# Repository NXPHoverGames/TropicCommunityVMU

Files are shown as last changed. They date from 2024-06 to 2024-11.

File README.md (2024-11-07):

# Tropic Community VMU

Tropic Community VMU (Vehicle Management Unit) is an BSD-3 Licensed Open-Source base board designed around the [Teensy 4.1 Development board](https://www.pjrc.com/store/teensy41.html).

> [!NOTE]  
> Tropic VMU is a project created by a group of passionate individuals who work on it in their free time. It's important for users to understand that Tropic might not provide the same reliability, features, or support as products from well-established companies. Using Tropic is entirely up to the user's discretion and comes with its own risks.
> 
> For a more dependable and professional VMU, we suggest looking into the NXP reference based on Dronecode Pixhawk standard V6X-RT (p/n MR-VMU-RT1176). The NXP V6X-RT offers advanced features, some level of support across multiple autopilots, and is designed towards the needs of professional users, providing a more reliable solution for their requirements.

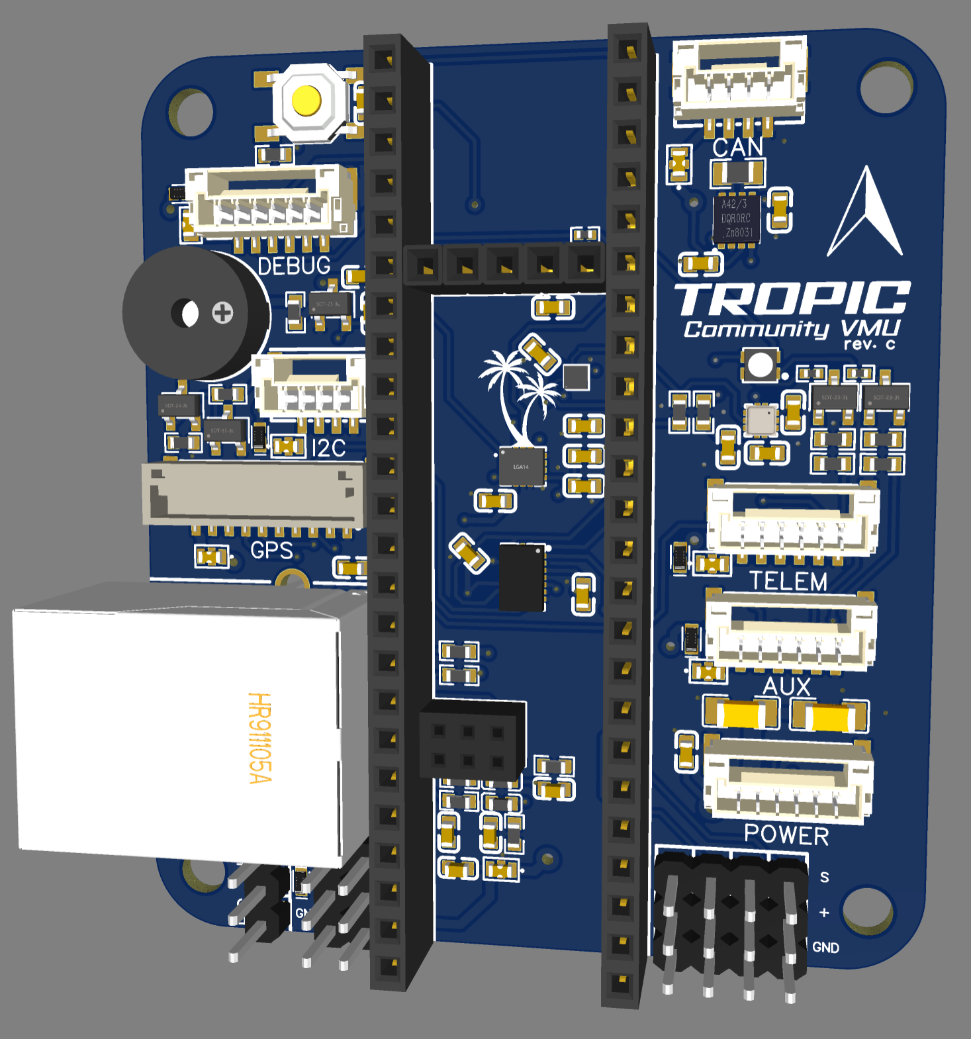
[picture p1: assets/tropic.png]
Tropic


Tropic Community VMU is capable of running autopilot software for unmanned vehicles such as:
 - Drones
 - Rovers
 - Boats
 - And more

## Drone Test flight Video

IMAGE ALT TEXT HERE (https://www.youtube.com/watch?v=fEz2vMWSv8o)

# Software

The Tropic Community VMU supports multiple Autopilots, please check the individual guide below

 - [Cognipilot setup guide](./Cognipilot.md)
 - [PX4 Autopilot setup guide](./PX4_Autopilot.md)

Tropic VMU also supports Zephyr RTOS with most of it's peripherals enabled.

> [!NOTE]  
> We're still in the process of upstreaming code please check the open pull requests in the corresponding projects

# Hardware

Tropic Community VMU utilizes the Teensy 4.1 consisting of:

- NXP MIMXRT1062DVJ6B MCU
- Cortex-M7 600MHz
- 1024K RAM (512 Tightly coupled)
- 8MB Flash
- 100Mbps Ethernet
- USB HS 480Mbit/s
- SD Card interface

Tropic Base board consisting of:

- Bosch BMI088 IMU
- Bosch BMM150 Magnetometer 
- Bosch BMP388 Barometer
- TDK InvenSense ICM-42688-P IMU
- NXP TJA1051TK CAN Transceiver
- RGB Led
- Buzzer
- Button

With connectors for:

- 10-pin JST-GH GPS connector
- 6-pin JST-GH UART + Handshake connector
- 6-pin JST-GH AUX Multi-function connector
    - UART
    - Quadrature decoder
    - PWM
    - Crossbar trigger
- 6-pin JST-GH Power module connector
    - [Tropic Power module](./tropic_power_module.md)
    - [Holybro PM02](https://holybro.com/products/pm02-v3-12s-power-module)
    - [Aliexpress PM06](https://nl.aliexpress.com/item/1005003265592048.html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)
- 6-pin JST-GH Debug UART connector providing system console
- 4-pin JST-GH I2C connector
- 4-pin JST-GH CAN bus connector
- 3-pin DuPont for Digital Receiver i.e. SBUS
- 6x 3-pin DuPont PWM header (DShot capable)
- RJ45 Ethernet connector

Some of the JST-GH connectors pinout follows the [DS-009 connector specification](https://github.com/pixhawk/Pixhawk-Standards/blob/master/DS-009%20Pixhawk%20Connector%20Standard.pdf)

# Powering the board

The Tropic Community VMU can be powered in 2 ways

> [!WARNING]  
> You should only power the Tropic Community VMU through either method 1. or 2. For example the current can flow from the power module to your usb potentially damaging your machine.
> You should to cut the power pad on the Teensy as a precaution if you want to use USB and the Power-module simultaneously, but by doing so you would lose the ability to power the board through USB.
> For more information see [Teensy External Power](https://www.pjrc.com/teensy/external_power.html) guide.

1. Through the micro-USB port on the Teensy 4.1
2. Through a 6-pin JST-GH power module

# Pinout

| Teensy Pin | Label | IMXRT Label | Peripheral | Alternative mode |
|---|---|---|---|---|
| 35 | TX DEBUG | B1_12 | LPUART5 | |
| 34 | RX DEBUG | B1_13 | LPUART5 | |
| 17 | TX TELEM | AD_B1_06 | LPUART3 | |
| 16 | RX TELEM | AD_B1_07 | LPUART3 | |
| 41 | TELEM RTS | AD_B1_05 | LPUART3 | GPIO1_IO21 |
| 40 | TELEM CTS | AD_B1_04 | LPUART3 | GPIO1_IO20 |
| 14 | TX GPS | AD_B1_03 | LPUART2 | |
| 15 | RX GPS | AD_B1_02 | LPUART2 | |
| 8 | TX AUX | B1_00 | LPUART4 | XBAR1_XBAR_IN14  |
| 7 | RX AUX | B1_01 | LPUART4 | XBAR1_XBAR_IN15  |
| 20 | RC | AD_B1_10 | LPUART8 | |
| 19 | EXT_SCL | AD_B1_00 | LPI2C1 | |
| 18 | EXT_SDA | AD_B1_01 | LPI2C1 | |
| 24 | BARO_MAG_SCL | AD_B0_12 | LPI2C4 | |
| 25 | BARO_MAG_SDA | AD_B0_13 | LPI2C4 | |
| 27 | SPI2_SCK | AD_B1_15 | LPSPI3 | |
| 26 | SPI2_MOSI | AD_B1_14 | LPSPI3 | |
| 39 | SPI2_MISO | AD_B1_13 | LPSPI3 | |
| 38 | SPI2_CS | AD_B1_12 | LPSPI3 | GPIO1_IO28 |
| 28 | DRDY | EMC_32 | LPSPI3 | GPIO3_IO18 |
| 13 | SPI1_SCK | B0_03 | LPSPI4 | |
| 11 | SPI1_MOSI | B0_02 | LPSPI4 | |
| 12 | SPI1_MISO | B0_01 | LPSPI4 | |
| 10 | SPI1_CS | B0_00 | LPSPI4 | GPIO2_IO00 |
| 36 | SPI1_CS2 | B1_02 | LPSPI4 | GPIO2_IO18 |
| 23 | BMI DRDY | AD_B1_09 | LPSPI4 | GPIO1_IO25 |
| 6 | BMI DRDY2 | B0_10 | LPSPI4 | GPIO2_IO10 |
| 4 | PWM_1 | EMC_06 | FLEXPWM2_PWMA00 | FLEXIO1_FLEXIO06 |
| 33 | PWM_2 | EMC_07 | FLEXPWM2_PWMB00 | FLEXIO1_FLEXIO07 |
| 5 | PWM_3 | EMC_08 | FLEXPWM2_PWMA01 | FLEXIO1_FLEXIO08 |
| 9 | PWM_4 | B0_11 | FLEXPWM2_PWMB02 | FLEXIO2_FLEXIO11 |
| 2 | PWM_5 | EMC_04 | FLEXPWM4_PWMA02 | FLEXIO1_FLEXIO04 |
| 3 | PWM_6 | EMC_05 | FLEXPWM4_PWMB02 | FLEXIO1_FLEXIO05 |
| 0 | LED_R | AD_B0_02 | XBAR1_XBAR_IN16 | GPIO1_IO02 |
| 1 | LED_B | AD_B0_03 | XBAR1_XBAR_IN17 | GPIO1_IO03 |
| 37 | LED_G | B1_03 | FLEXPWM2_PWMB03 | GPIO2_IO19 |
| 29 | BUZZER | EMC_31 | FLEXPWM3_PWMA01 | GPIO4_IO31 |
| 32 | ARM | B0_12 | GPIO | GPIO2_IO12 |
| 22 | ADC_V | AD_B1_08 | ADC1_IN13 | GPIO1_IO27 |
| 21 | ADC_A | AD_B1_11 | ADC1_IN0 | GPIO1_IO24 |

# Open-source hardware Design

Tropic Community VMU design is licensed under BSD-3 and all design files are published on this git.

## Schematics
[Tropic Community VMU rev.C schematics](./schematics/Schematic_Tropic-VMU_2024-05-31_revC.pdf)

## PCB Design

The board is designed using [EasyEda Std Edition](https://easyeda.com/editor), to import the project you've to create a new project in EasyEda Std edition and select File -> Open -> EasyEda and select the json files available in the zip file.

[Tropic Community VMU rev.C EasyEda zip file](./board/tropic_vmu_easyeda_revc.zip)

## Bill-of-Material (BOM)

Click here for the [BOM](./BOM.md)

## Production files

These are the [production files](./board/tropic_vmu_production_files_revc.zip) used for rev.C of tropic

## Printable models/parts

For 3d-printed enclosures and parts checkout the [Printable models/parts](./printable_models.md) page

## Advanced topics

Some advanced topics regarding Ethernet, RTC and AUX port are explained [here](./advanced_topics.md)

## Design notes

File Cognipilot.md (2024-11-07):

# Cognipilot
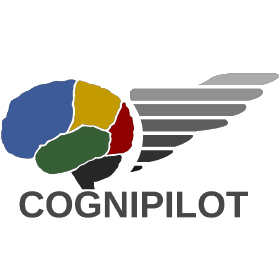
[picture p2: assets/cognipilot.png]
Cognipilot


CogniPilot is a new class of open source autopilot that can conduct safety critical missions such as public transport, with a level of safety assurance not currently available in other open source autopilots. CogniPilot focuses on state-of-the-art methodologies for creating an autopilot with mathematically provable robustness properties.

For more information on how to setup your environment and build cognipilot checkout the [Cognipilot developers guide](https://cognipilot.org/)

# Flashing the board

The Teensy comes with its own bootloader, allowing to flash Cerebri through USB.
Teensy provides a Teensy Loader gui flashing for more information checkout their [guide](https://www.pjrc.com/teensy/loader.html)

On Linux you can also flash Cerebri directly from the `west` build system.
To use this method, first install the `teensy-loader-cli` application.
On a Ubuntu based system you can use the following command

```sudo apt install teensy-loader-cli```

Connect the board through USB and then press the physical button on the Teensy to put it into bootloader mode.

Flashing the board is simply done by the command below

```west flash```

On success you should get the following output

```
-- west flash: rebuilding
[1/1] cd /home/peter/cognipilot/ws/cerebri/build/zephyr &&...=/home/peter/cognipilot/ws/cerebri/build/zephyr/zephyr.elf
/home/peter/cognipilot/ws/cerebri/build/zephyr/runners.yaml
flash-runner
-- west flash: using runner teensy
-- runners.teensy: Flashing file: /home/peter/cognipilot/ws/cerebri/build/zephyr/zephyr.hex
```

If Cognipilot has been succesfully flash you should hear a startup tone from buzzer.

# Serial Console 

By default the Cerebri Serial console is provided through `lpuart` on the 6-pin JST-GH connector labeled Debug.
```
                                          ▄▄▄▄▄▄▄▄
         ▄▄▄▄▄ ▄▄▄▄▄                    ▀▀▀▀▀▀▀▀▀
     ▄███████▀▄██████▄   ▀█████████████████████▀
  ▄██████████ ████████ ▄   ▄▄▄▄▄▄▄▄▄▄▄▄▄▄▄▄▄▄
 ███████████▀ ███████▀ ██   ▀▀▀▀▀▀▀▀▀▀▀▀▀▀▀▀
█████████▀   ▀▀▀▀▀▀▀▀ ████   ▀███████████▀
▀█████▀ ▄▄███████████▄ ████   ▄▄▄▄▄▄▄▄▄
  ▀▀▀ ███████████████▀ ████   ▀▀▀▀▀▀▀▀
       ▀▀█████▀▀▀▀▀▀  ▀▀▀▀   ▄█████▀
               ████████▀    ▄▄▄
               ▀███▀       ▀▀▀
                ▀▀
╔═══╗╔═══╗╔═══╗╔═╗ ╔╗╔══╗╔═══╗╔══╗╔╗   ╔═══╗╔════╗
║╔═╗║║╔═╗║║╔═╗║║║║ ║║╚╣╠╝║╔═╗║╚╣╠╝║║   ║╔═╗║║╔╗╔╗║
║║ ╚╝║║ ║║║║ ╚╝║║╚╗║║ ║║ ║║ ║║ ║║ ║║   ║║ ║║╚╝║║╚╝
║║   ║║ ║║║║╔═╗║╔╗╚╝║ ║║ ║╚═╝║ ║║ ║║   ║║ ║║  ║║
║║ ╔╗║║ ║║║║╚╗║║║╚╗║║ ║║ ║╔══╝ ║║ ║║ ╔╗║║ ║║  ║║
║╚═╝║║╚═╝║║╚═╝║║║ ║║║╔╣╠╗║║   ╔╣╠╗║╚═╝║║╚═╝║ ╔╝╚╗
╚═══╝╚═══╝╚═══╝╚╝ ╚═╝╚══╝╚╝   ╚══╝╚═══╝╚═══╝ ╚══╝
       ┏━━━┓┏━━━┓┏━━━┓┏━━━┓┏━━┓ ┏━━━┓┏━━┓
       ┃┏━┓┃┃┏━━┛┃┏━┓┃┃┏━━┛┃┏┓┃ ┃┏━┓┃┗┫┣┛
       ┃┃ ┗┛┃┗━┓ ┃┗━┛┃┃┗━┓ ┃┗┛┗┓┃┗━┛┃ ┃┃
       ┃┃ ┏┓┃┏━┛ ┃┏┓┏┛┃┏━┛ ┃┏━┓┃┃┏┓┏┛ ┃┃
       ┃┗━┛┃┃┗━━┓┃┃┃┗┓┃┗━━┓┃┗━┛┃┃┃┃┗┓┏┫┣┓
       ┗━━━┛┗━━━┛┗┛┗━┛┗━━━┛┗━━━┛┗┛┗━┛┗━━┛
*** Booting Zephyr OS build zephyr-v3.5.0-3936-g9e01bfe86b7c ***
uart:~$
```
On bootup you should see this Cognipilot banner and then you get a `uart:~$` shell to type your commands

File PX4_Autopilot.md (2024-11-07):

# PX4 Autopilot

PX4 is an open-source BSD-3 Licensed autopilot system for unmanned aerial vehicles (UAVs) It provides both hardware and software components to control various types of drones, from small quadcopters to fixed-wing aircraft and even autonomous vehicles like rovers and boats.

# Tropic Community VMU PX4 Known Issues 

Some PX4 features are **not** fully integrated and are still work-in-progress.
 
- PWM_4 Doesn't support DShot, however PWM_1, PWM_2, PWM_3, PWM_5 and PWM_6 do work fine.
  - PWM_4 uses FlexIO2 instead of FlexIO1, needs driver modification for it to work.

# Serial port mapping

| UART | Device | Port  |
|---|---|---|
| LPUART5 | /dev/ttyS0 | DEBUG |
| LPUART3 | /dev/ttyS2 | TELEM |
| LPUART2 | /dev/ttyS1 | GPS |
| LPUART4 | /dev/ttyS3 | AUX |
| LPUART8 | /dev/ttyS4 | RC |

# Building PX4 for Tropic Community VMU

> [!NOTE]  
> Nov 7th, 2024 as of now PX4 main includes the nxp_tropic-community target

First you need to setup your build environment. The PX4 user guide provides a [Developer Environment guide](https://docs.px4.io/main/en/dev_setup/dev_env.html). There you can select the corresponding guide for your platform, [Ubuntu](https://docs.px4.io/main/en/dev_setup/dev_env_linux_ubuntu.html), [Windows](https://docs.px4.io/main/en/dev_setup/dev_env_windows_wsl.html), [macOS](https://docs.px4.io/main/en/dev_setup/dev_env_mac.html).

After setting up your build environment enter the `PX4-Autopilot` folder and type the following command to build PX4
```
make nxp_tropic-community
```

# Flashing the board

The Teensy comes with it's own bootloader, allowing to flash PX4 through USB.
Teensy provides a Teensy Loader gui flashing for more information checkout [this guide](https://www.pjrc.com/teensy/loader.html). The file you want to flash is located under `PX4-Autopilot/build/nxp_tropic-community_default/nxp_tropic-community_default.hex`

On Linux you can also flash PX4 directly from the `make` build system.
Make sure to install the `teensy-loader-cli` application first.
On a Ubuntu based system you can use the following command

```
sudo apt install teensy-loader-cli
```

Connect the board through USB and then press the physical button on the Teensy to put it into bootloader mode.

Flashing the board is simply done by the command below

```
make nxp_tropic-community upload_teensy
```

A succesfull flash should like like this.

```
peter@desktop-peter:~/src/firmware$ make nxp_tropic-community upload_teensy
[0/1] uploading px4
Found teensy bootloader
Teensy Loader, Command Line, Version 2.2
Read "/home/peter/src/PX4-Autopilot/build/nxp_tropic-community_default/nxp_tropic-community_default.hex": 1809658 bytes, 22.3% usage
Found HalfKay Bootloader
Programming........................................................................................
Booting
peter@desktop-peter:~/src/PX4-Autopilot$
```

# QGroundControl

Once PX4 has been flashed on the Tropic Community VMU, Connect the Tropic Community VMU to your PC through USB and launch [QGroundControl](http://qgroundcontrol.com/) to configure your Tropic Community VMU.

For more information on how to configure PX4 checkout the [PX4 configuration guide](https://docs.px4.io/main/en/config/)

# PX4 Tropic Community VMU rev. A test

The first revision of the Tropic Community VMU rev.A has been tested with PX4 has been tested on a small quad in autonomous flight.

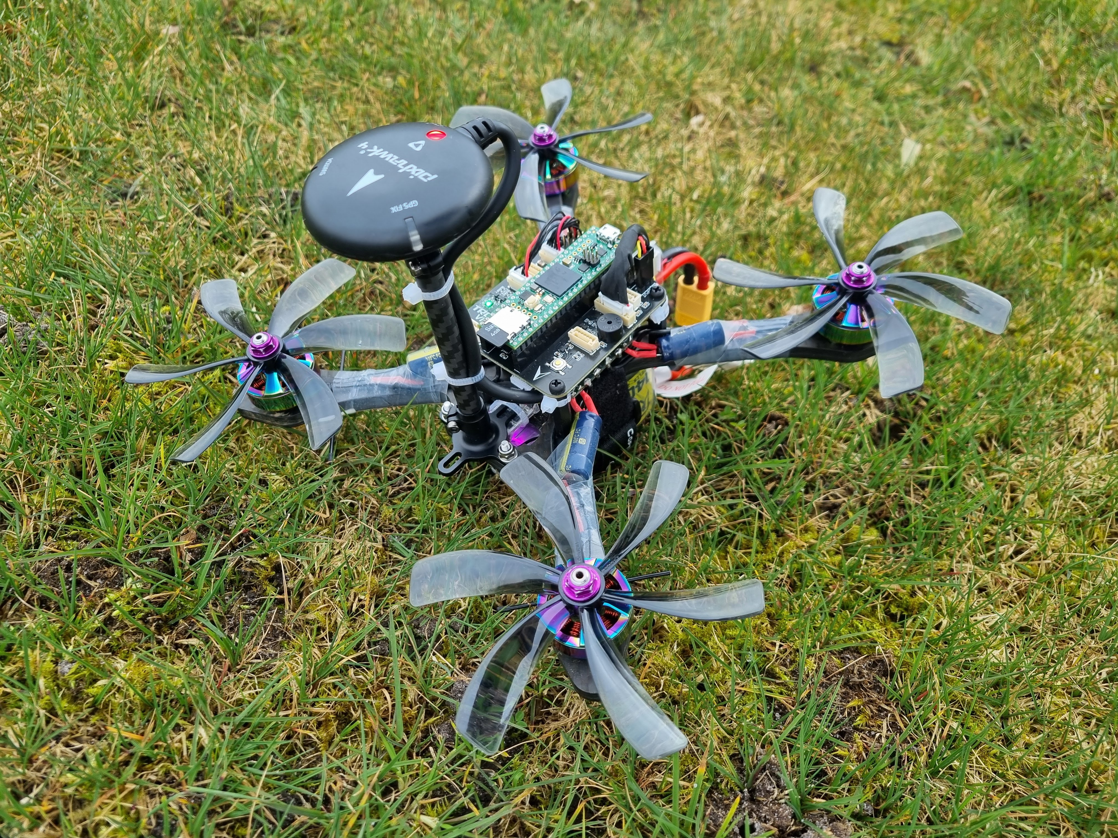
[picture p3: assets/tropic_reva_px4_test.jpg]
PX4 Tropic Community VMU Test drone


## PX4 Testing Flight Logs:
1. https://logs.px4.io/plot_app?log=9d5c333c-3806-461c-9c77-20e4f58b2683
2. https://logs.px4.io/plot_app?log=161a0efc-d6a4-471e-990d-6fe45f177ba8

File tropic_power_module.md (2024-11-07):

# Tropic Power Module

Tropic Power Module is an BSD-3 Licensed Open-Source board designed for the [Tropic Community VMU (Vehicle Management Unit)](./README.md)
It provides analog measurement of voltage and current which can be used by flight control software to estimate the battery state and/or power consumption.

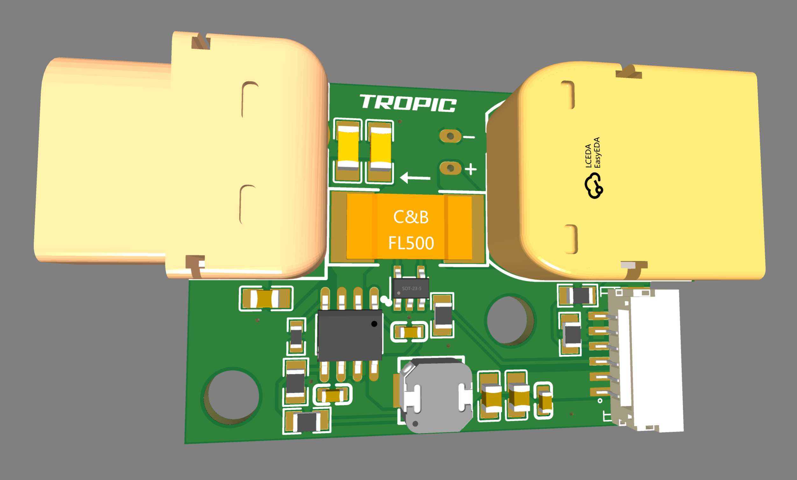
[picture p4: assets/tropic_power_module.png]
Tropic


# Hardware

Tropic Power Module Specification:

- 6.4-36V Input voltage (2S-8S)
- 5.3V Max. 3A output
- Voltage Divider: 18
- Amperes per volt: 38.462A

Power module JST-GH 6-pin pinout:

| JST-GH Pin | Label |
|---|---|
| 1 | 5V |
| 2 | 5V |
| 3 | ADC_A |
| 4 | ADC_V |
| 5 | GND |
| 6 | GND |

## Schematics
[Tropic Power Module rev.A schematics](./schematics/Schematic_Tropic-PM_2024-03-21_revA.pdf)

## PCB Design

The board is designed using [EasyEda Std Edition](https://easyeda.com/editor), to import the project you've to create a new project in EasyEda Std edition and select File -> Open -> EasyEda and select the json files available in the zip file.

[Tropic Power Module rev.A EasyEda zip file](./board/tropic_pm_easyeda_reva.zip)

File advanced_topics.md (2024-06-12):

# Tropic VMU Advanced Topics

This page describes various topics for advanced users.

# Ethernet

> [!WARNING]  
> For those with a Tropic VMU rev.B baseboard the RJ45 is non-fuctional, please use rev.C or later for ethernet

## Ethernet 3x2 Socket + Pins

The ethernet board-to-board connection is a 3x2 socket with a 2mm pitch. Conventional 2x3 2mm pitch female headers should work fine but male headers have to be taller (~ 8.5mm) [PJRC provides Pins & Sockets](https://www.pjrc.com/store/header_socket_3x2.html) with the correct size.

As alternative you can also get these Pins from a distributor: \
Samtec MTMM-103-10-T-D-355

Or these sockets: \
TE 2314820-6 \
BOOMELE(Boom Precision Elec) 2.0-2*3P 

# Real-time Clock (RTC) Circuitry

A RTC allows you to keep track on time while the Tropic is powered off.
This is done by powering the [VBAT pin](https://www.pjrc.com/store/teensy41.html#power) on the Teensy with a battery which allows the Tropic to keep track of time without power.

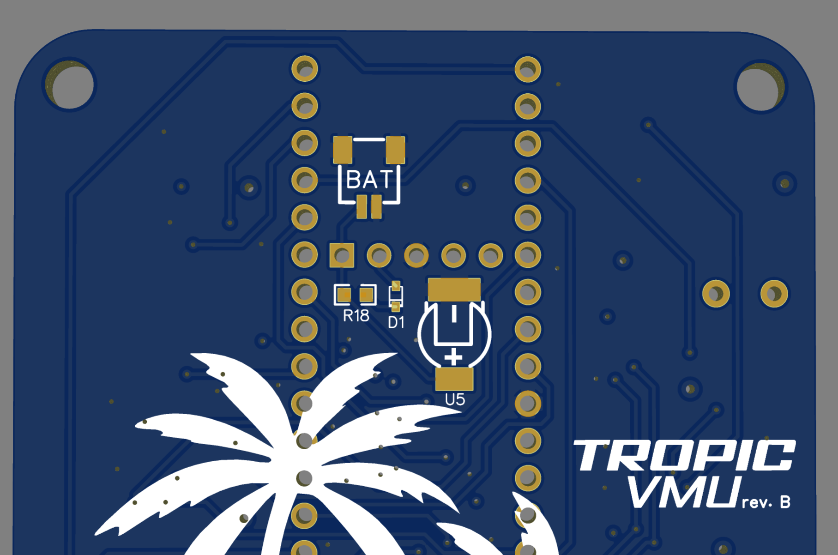
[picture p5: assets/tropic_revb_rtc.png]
Tropic


The Tropic baseboard allows to 3 ways to power VBAT.
- The combination of D1 and R18 are used to provide an adjustable trickle charge to a supercap or rechargeable battery
1. **SuperCap**: By placing a supercap (DSK-3R3H703T414-HRL) on U5, diode (PMEG4002EB) on D1 and a 300Ω resistor on R18
   
2. **Rechargeable Battery**: An external ML2020 rechargeable battery connected with a JST-SH connector for example the [Raspberry Pi RTC battery](https://www.raspberrypi.com/products/rtc-battery/). By placing a JST-SH 2-pin connector (SM02B-SRSS-TB (LF)(SN)) on BAT, diode (BAT43XV2) on D1 and a 300Ω resistor on R18.
  
3. **Primary Lithium Cell**: An external CR2032 battery, By placing a JST-SH 2-pin connector (SM02B-SRSS-TB (LF)(SN)) on BAT, do not populate R18 and D1.

# AUX Port

The AUX port is a 6-pin JST-GH Multi-function connector capable of the following configurations:
- 1x UART using pin 2,3 and with pin4,5 claimed by RGB led
- 2x UART
- 1x UART with GPIO Handshaking
- Quadrature decoder
- 4x PWM
- Crossbar trigger

JST-GH 6-pin pinout:

| JST-GH Pin | Label | IMXRT Label |
|---|---|---|
| 1 | 5V | - |
| 2 | TX AUX | B1_00 |
| 3 | RX AUX | B1_01 |
| 4 | LED_R | AD_B0_02 |
| 5 | LED_B | AD_B0_03 |
| 6 | GND | - |

> [!NOTE]  
> Pin 4,5 on the AUX connector are shared with LED_R and LED_B from the RGB Led, you can only use either at the same time

This table shows the alternative MCU(Teensy Pin) functions available on AUX Port pins 2,3,4,5 above.

| Teensy Pin | Label | IMXRT Label | Primary Mode | Alternative modes |
|---|---|---|---|---|
| 8 | TX AUX | B1_00 | LPUART4_TX | FLEXPWM1_PWMA03, XBAR1_XBAR_IN14, GPIO2_IO16  |
| 7 | RX AUX | B1_01 | LPUART4_RX | FLEXPWM1_PWMB03, XBAR1_XBAR_IN15, GPIO2_IO17  |
| 0 | LED_R | AD_B0_02 | XBAR1_XBAR_IN16 | LPUART6_TX, XBAR1_XBAR_IN16, GPIO1_IO02 |
| 1 | LED_B | AD_B0_03 | XBAR1_XBAR_IN17 | LPUART6_RX, XBAR1_XBAR_IN17, GPIO1_IO03 |

## PX4 AUX configuration
In the PX4 the AUX connector is configured by default to be a single UART with LED_R, LED_B used for the RGB led. Due note when connecting a 6-pin UART device **you will need to unplug** pin 4 and pin 5 to otherwise your device will receive interference from the RGB led PWM.

# BMP388 End-of-life

The BMP388 Barometer availability is declining due to its EOL status. However the new BMP390 is pin-compatible and should just work fine as a replacement.

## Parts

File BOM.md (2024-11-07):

# Tropic Community VMU revC BOM

| Top Designator | Comment | Footprint | Part number |
|---|---|---|---|
| ARMING_BUTTON1 | TS-1187A-B-A-B | SW-SMD_4P-L5.1-W5.1-P3.70-LS6.5-TL-2 | TS-1187A-B-A-B |
| AUX,DEBUG,POWER,TELEM | BM06B-GHS-TBT(LF)(SN)  | CONN-SMD_BM06B-GHS-TBT-LF-SN | BM06B-GHS-TBT(LF)(SN) |
| BUZZER1 | QMB-09B-03 | BUZ-TH_BD9.0-P4.00-D0.6-FD | QMB-09B-03 |
| C1,C2,C3,C6,C13,C14,C15,C16,C20,C21,C23,C34,C39 | 100nF | C0603 | GCM188R71H104KA57D |
| C4,C8,C9,C24,C25,C26,C27 | NFM18PC104R1C3D | FILTER-SMD_3P-L1.6-W0.8-L_NFM18CC223R1C3D  | NFM18PC104R1C3D |
| C5,C7 | 47uF | C1206 | CL31A476MPHNNNE |
| C11,C38 | 2.2nF | C0603 | 0603B222K500NT |
| C12 | 10nF | C0603 | 0603B103K500NT |
| C17,C18 | 1000pF | C0603 | CL10B102KB8NNNC |
| C28,C29 | 4.7uF | C0603 | 0603B152K500NT 
| CAN,I2C | A1257WV-S-4P | CONN-SMD_A1257WV-S-4P | A1257WV-S-4P-LCP |
| D5,D6,D7,D8,D9 | PMEG2020EPK,315 | SOD1608_L1.6-W0.8-LS1.6-RD | PMEG2020EPK,315 |
| F1 | 0603-025 | F0603 | SMD0603-025 |
| GPS | BM10B-GHS-TBT(LF)(SN)  | CONN-SMD_BM10B-GHS-TBT-LF-SN | BM10B-GHS-TBT(LF)(SN) |
| H1,H2,H3,H4,H5,H6,RC_INPUT | PZ254V-11-03P_C2937625 | HDR-TH_3P-P2.54-V-M | PZ254V-11-03P |
| H7 | X6511FV-05-C85D32 | HDR-TH_5P-P2.54-V-F | X6511FV-05-C85D32 |
| L1,L2 | 10uH | L0603 | SDFL1608S100KTF |
| LED1 | FM-B2020RGBA-HG | LED-SMD_FM-B2020RGBA-HG | FM-B2020RGBA-HG |
| Q1,Q2,Q3,Q4 | AO3400A | SOT-23-3_L2.9-W1.6-P1.90-LS2.8-BR | AO3400A |
| R1,R2,R12,R13 | 4.7KΩ | R0603 | 0603WAF4701T5E |
| R3 | 120Ω | R0603 | 0603WAF1200T5E |
| R4,R23 | 75Ω | R0603 | 0603WAF750JT5E |
| R5,R8,R10,R19,R20 | 10kΩ | R0603 | 0603WAF1002T5E |
| R6 | 15kΩ | R0402 | 0402WGF1502TCE |
| R7,R9,R11 | 1kΩ | R0603 | 0603WAF1001T5E |
| R14 | 162Ω | R0402 | 0402WGF1620TCE |
| R15 | 60.4Ω | R0402 | 0402WGF604JTCE |
| R16 | 100Ω | R0402 | 0402WGF1000TCE |
| R17 | 120Ω | R0805 | RK73H2ATTD1200F |
| R21,R22 | 1.0MΩ | R0603 | 0603WAF1004T5E |
| J1 | HR911105A | RJ45-TH_HR911105A | HR911105A |
| U2 | ICM-42688-P | LGA-14_L3.0-W2.5-P0.50-TL | ICM-42688-P |
| U3 | BMM150 | WLCSP-12_L1.6-W1.6_BMM150 | BMM150 |
| U4 | BMI088 | LGA-16_L4.5-W3.0-P0.50-BL | BMI088 |
| U6 | TJA1051TK/3/1J | HVSON-8_L3.0-W3.0-P0.65-BL-EP | TJA1051TK/3/1J |
| U7,U8 | X6511FV-24-C85D32 | HDR-TH_24P-P2.54-V-F | X6511FV-24-C85D32 |
| U9 | XC6206P332MR | SOT-23-3_L2.9-W1.6-P1.90-LS2.8-BR | XC6206P332MR |
| U13 | BMP388 | SENSORM-SMD_BMP388 | BMP388 |
| U11 | 2*3P | HDR-TH_6P-P2.00-V-F-R2-C3-S2.00 | C110428 |

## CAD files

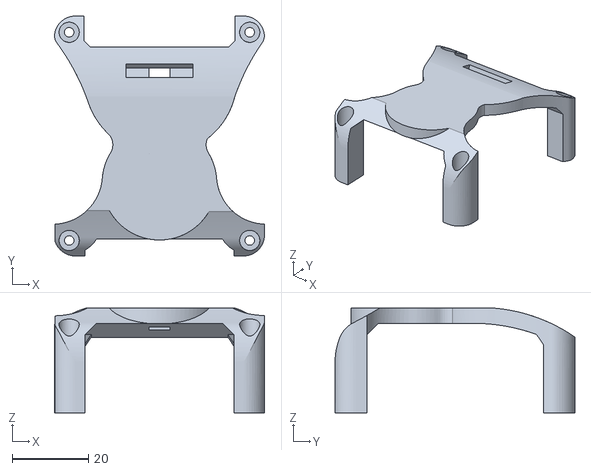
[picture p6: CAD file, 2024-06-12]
printable_models/gps_mount.stl
55.0 x 62.8 x 27.4

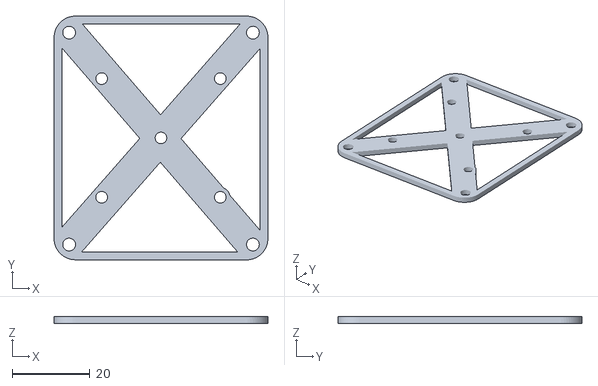
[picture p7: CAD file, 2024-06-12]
printable_models/tropic_drill_jig.stl
55.0 x 62.7 x 1.70

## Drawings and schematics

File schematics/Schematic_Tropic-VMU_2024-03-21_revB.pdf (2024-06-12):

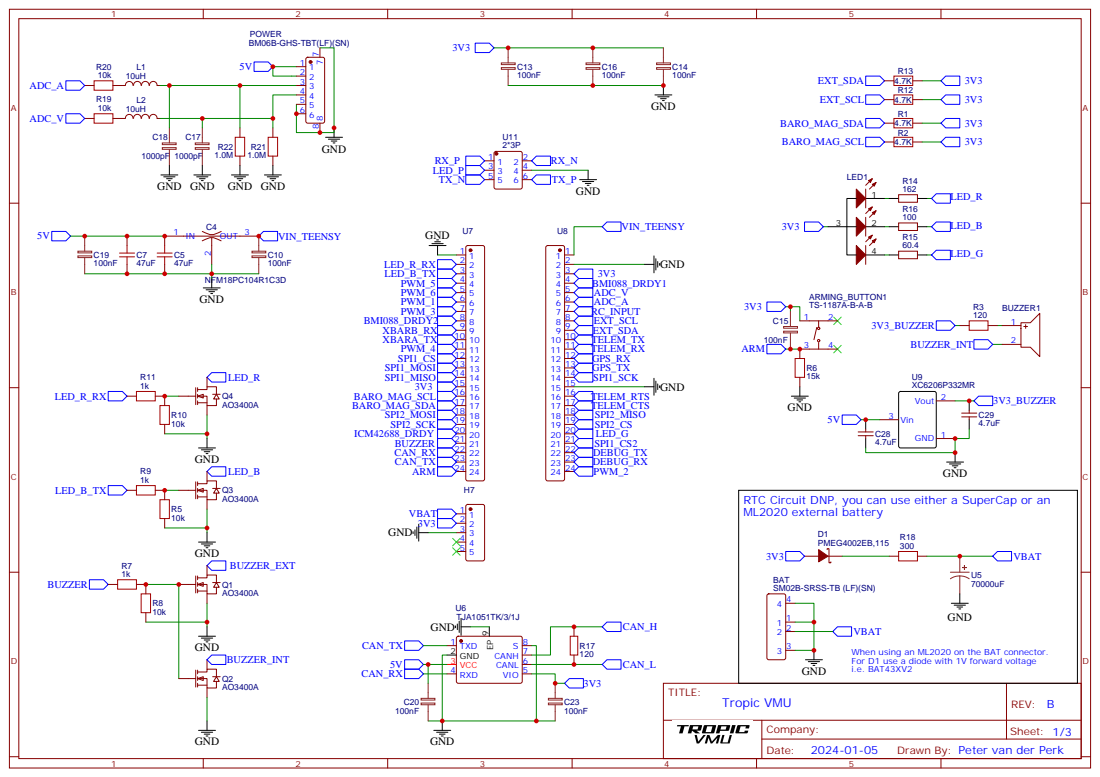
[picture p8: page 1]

POWER
BM06B-GHS-TBT(LF)(SN)

RTC Circuit DNP, you can use either a SuperCap or an
ML2020 external battery

When using an ML2020 on the BAT connector.
For D1 use a diode with 1V forward voltage
i.e. BAT43XV2

Drawn By: Peter van der Perk

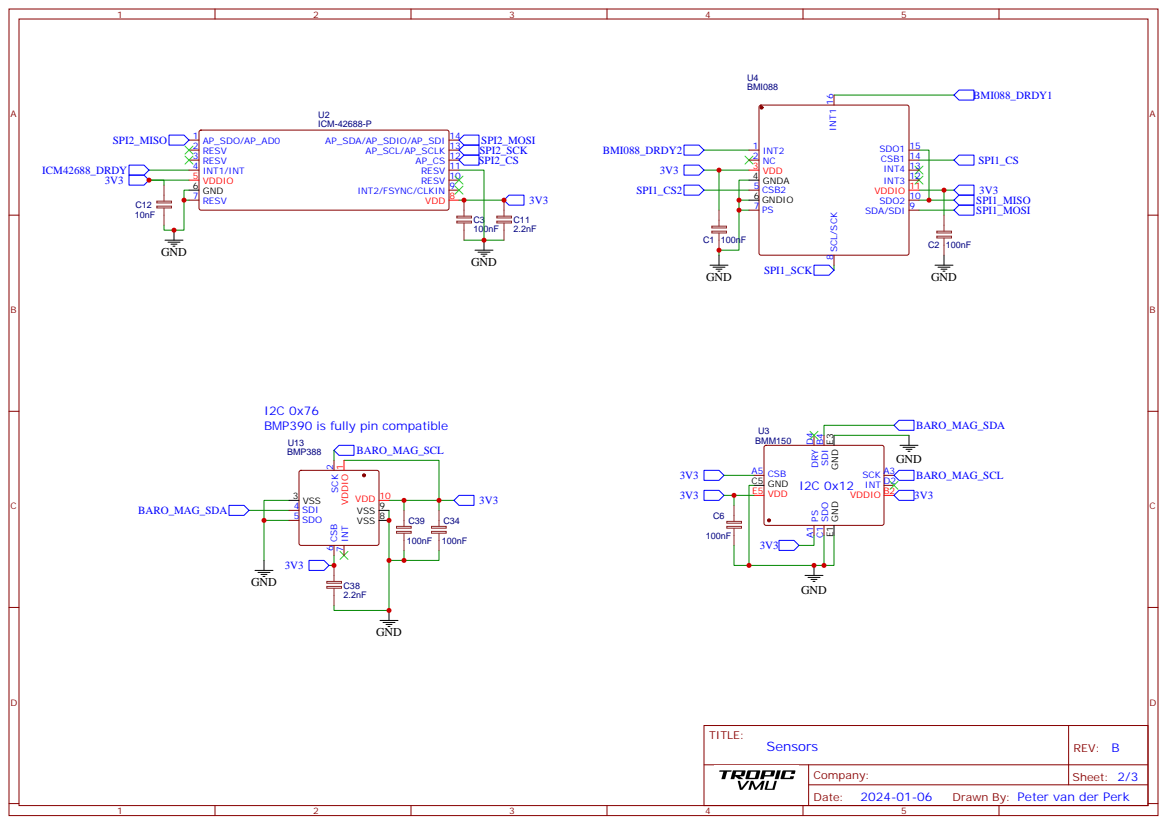
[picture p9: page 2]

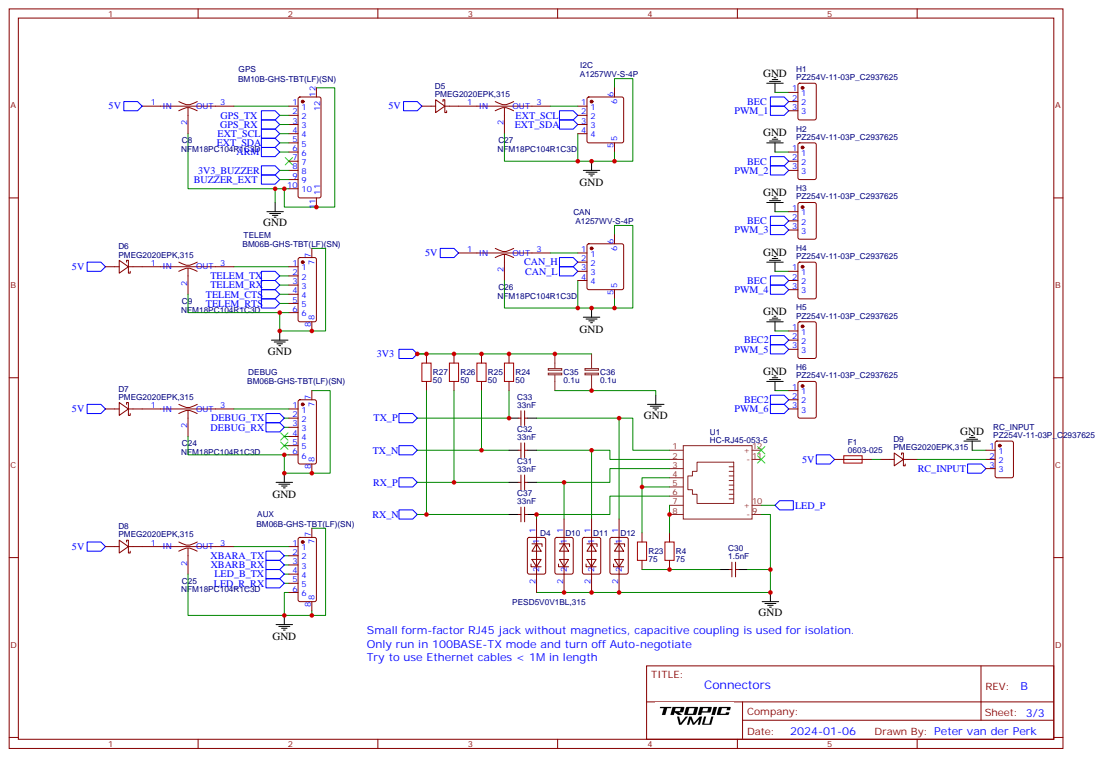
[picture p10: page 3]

GPS
BM10B-GHS-TBT(LF)(SN)

GND
TELEM
BM06B-GHS-TBT(LF)(SN)

DEBUG

AUX

Small form-factor RJ45 jack without magnetics, capacitive coupling is used for isolation.
Only run in 100BASE-TX mode and turn off Auto-negotiate
Try to use Ethernet cables < 1M in length

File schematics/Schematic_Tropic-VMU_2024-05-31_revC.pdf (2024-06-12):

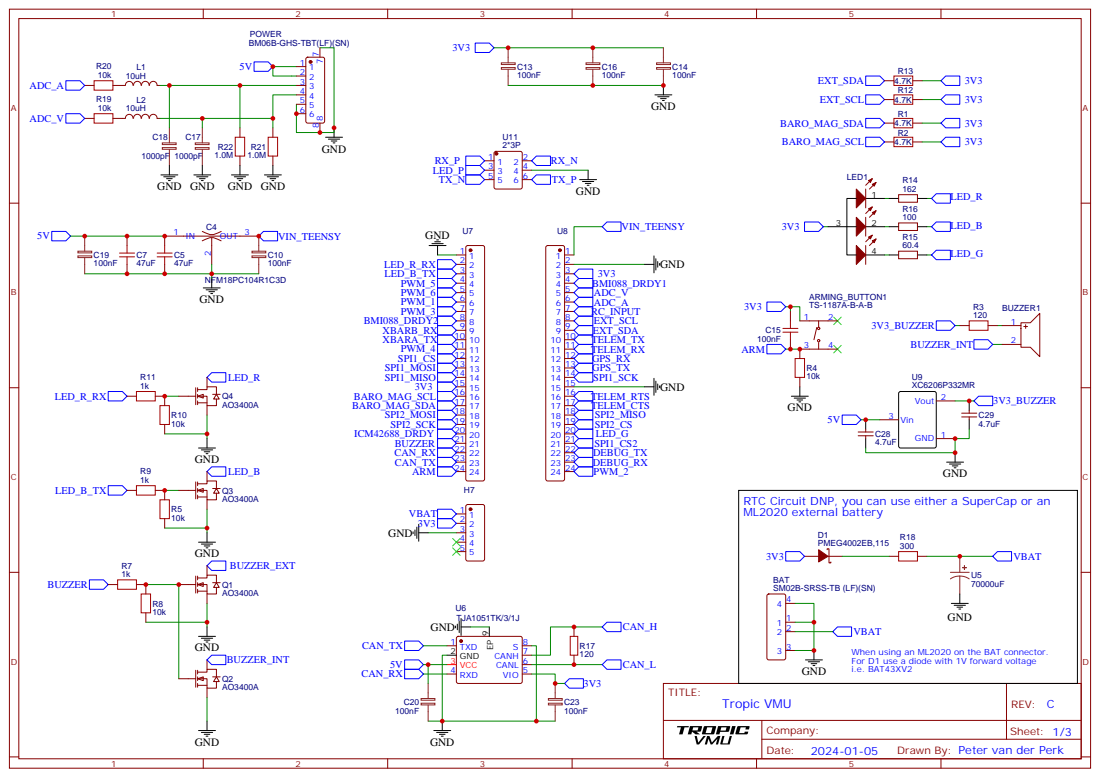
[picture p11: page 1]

POWER
BM06B-GHS-TBT(LF)(SN)

RTC Circuit DNP, you can use either a SuperCap or an
ML2020 external battery

When using an ML2020 on the BAT connector.
For D1 use a diode with 1V forward voltage
i.e. BAT43XV2

Drawn By: Peter van der Perk

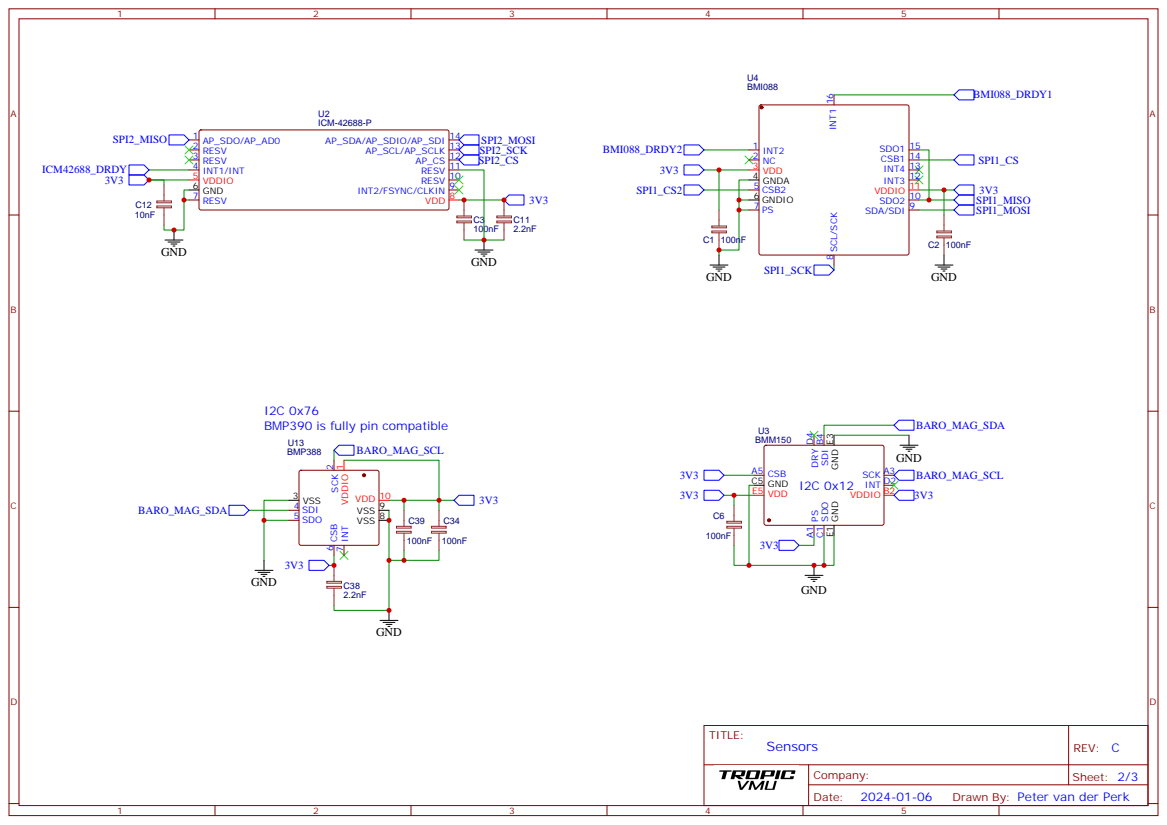
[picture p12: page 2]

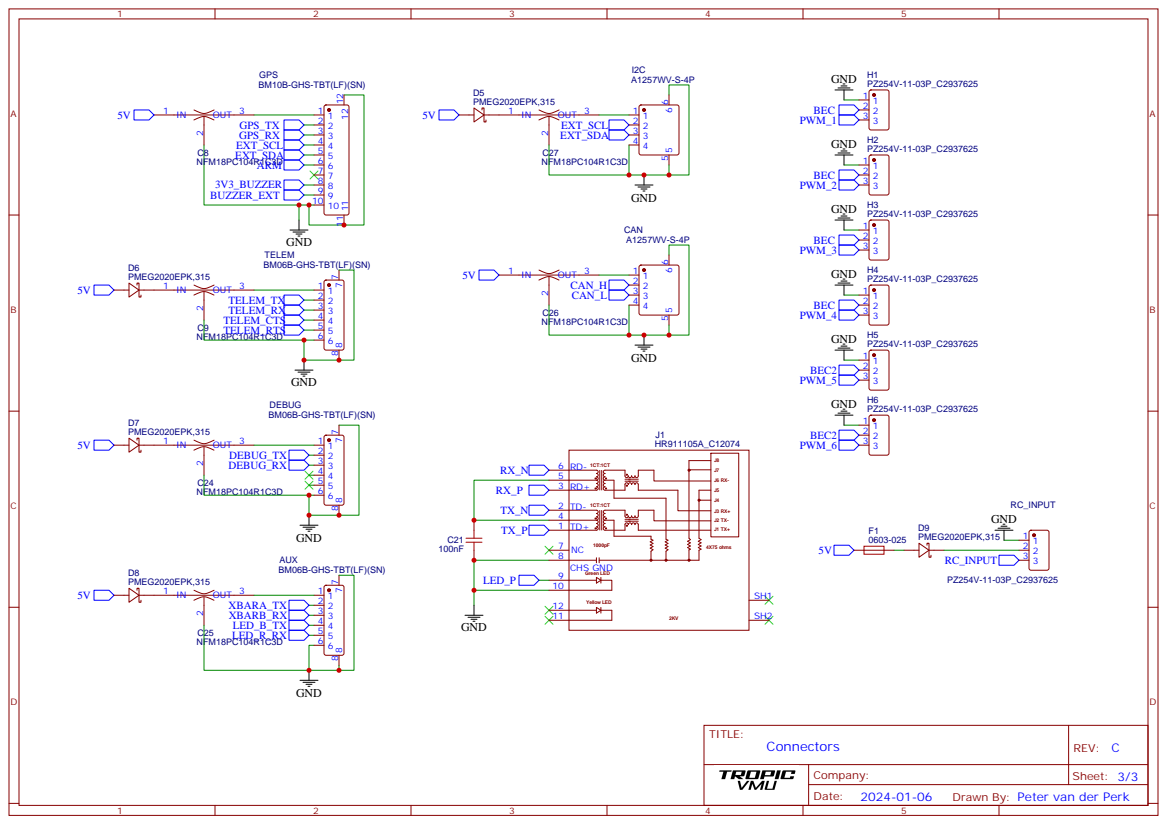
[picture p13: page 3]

GPS
BM10B-GHS-TBT(LF)(SN)

GND
TELEM
BM06B-GHS-TBT(LF)(SN)

DEBUG

AUX

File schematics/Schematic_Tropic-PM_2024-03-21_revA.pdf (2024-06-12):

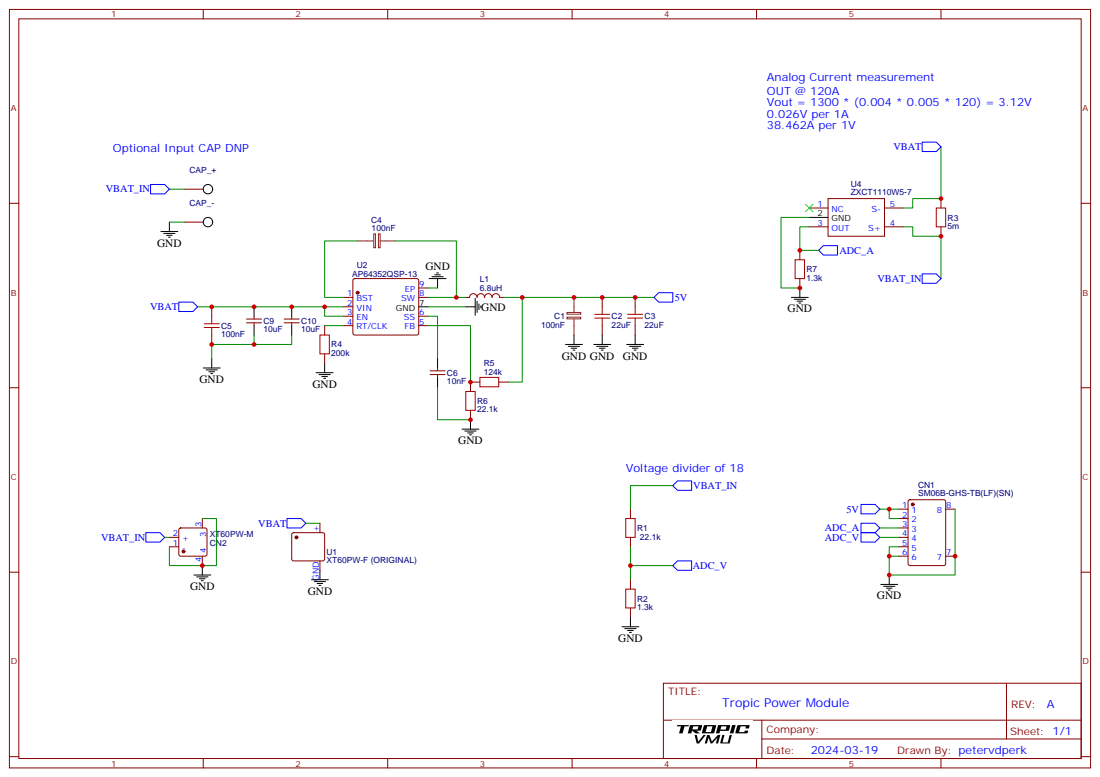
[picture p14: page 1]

Optional Input CAP DNP

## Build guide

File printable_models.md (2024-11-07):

# GPS Mount 

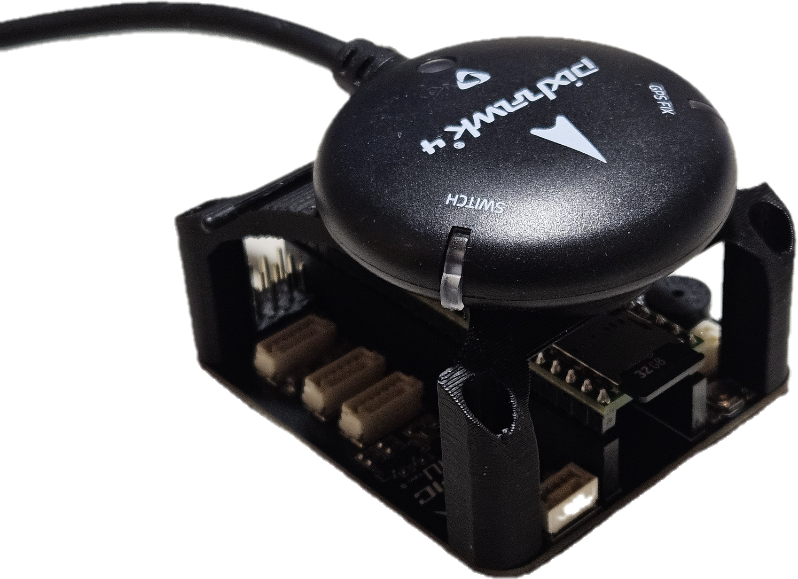
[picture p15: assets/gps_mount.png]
PX4 Tropic Community VMU GPS Mount

[3d-printed mount](./printable_models/gps_mount.stl) for GPS mounting i.e. [Holybro M10 GPS](https://holybro.com/collections/gps/products/m10-gps)

# Drill Jig

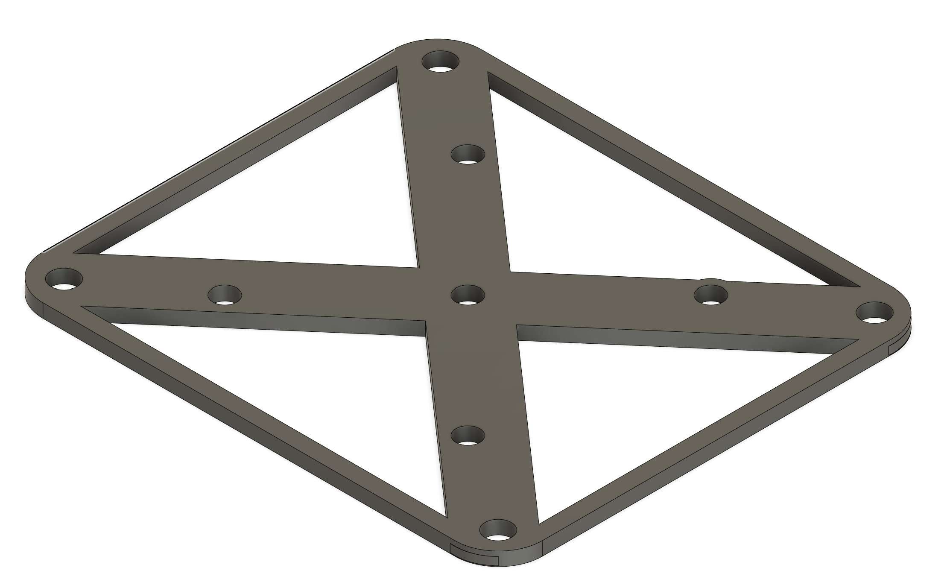
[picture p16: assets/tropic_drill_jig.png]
PX4 Tropic Community Drill Jig

[3d-printed jig](./printable_models/tropic_drill_jig.stl) for drilling the holes matching the Tropic  Community VMU baseboard holes
